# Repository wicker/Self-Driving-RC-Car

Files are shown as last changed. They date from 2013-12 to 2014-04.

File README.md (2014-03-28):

Self-Driving-RC-Car
===================

Testing out Kalman filter and SLAM code on a vehicle which can't fall out of the sky.

Hardware
--------

IMX (Imex) Firefox 1/10 scale RC car contains one RC550 brushed hobby DC motor and one three-wire RadioShack hobby servo. 

v1 controller is an Arduino Uno with VNH5019 Dual Motor Driver Carrier Shield from Pololu. 

v2 controller is an STM32F4-Discovery board with VNH5019 Dual Motor Driver Carrier shield from Pololu.

v3 controller is a custom Foxcar Control Board v1.

v4 controller is a custom Foxcar Control Board v2.

Software
--------

**v1 - Arduino**

A simple Arduino sketch to drive the motor in forward and reverse while turning the servo to steer the vehicle. Libraries used:

- [Zambetti's ASCIITable](http://arduino.cc/en/Tutorial/ASCIITable)
- [SoftwareSerial](http://arduino.cc/en/Reference/SoftwareSerial)
- [mem's ServoTimer2](http://forum.arduino.cc/index.php/topic,21975.0.html)
- [Pololu's VNH5019 Motor Driver Shield](https://github.com/pololu/dual-vnh5019-motor-shield)

**v2 - STM32F4-Discovery**

Putting everything together. 

- [Pololu's VNH5019 Motor Driver Shield](https://github.com/pololu/dual-vnh5019-motor-shield)

License
-------

Released under the 3-clause BSD. http://opensource.org/licenses/BSD-3-Clause

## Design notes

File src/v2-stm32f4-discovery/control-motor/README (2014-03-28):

INSTRUCTIONS

Add toolchain paths:

alias psas_stm="export PATH=$PATH:/opt/psas/openocd/bin:/opt/psas/x-tools/stm32f407/arm-psas-eabi/bin:/opt/eclipse/"

In this directory, modify the duration of the blinking LED pauses in main.c. 

Then:

make
st-flash write build/ch.bin 0x08000000.

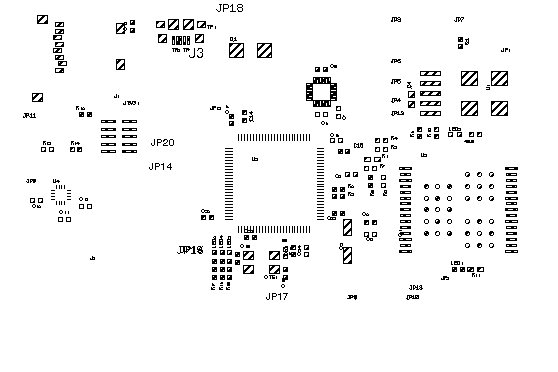
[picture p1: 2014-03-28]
sch/output.png

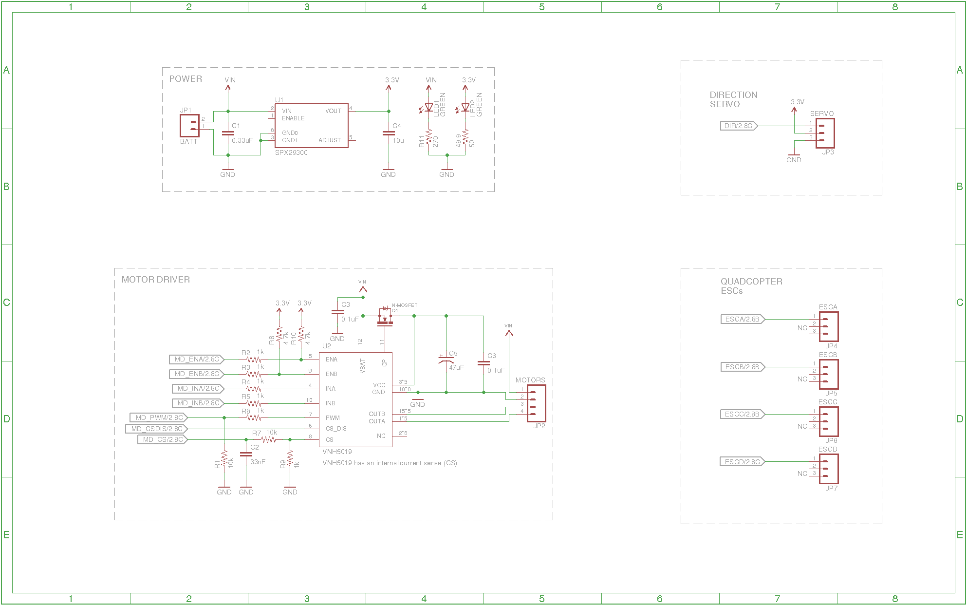
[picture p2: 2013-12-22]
sch/foxcar-control-board-sch1.png

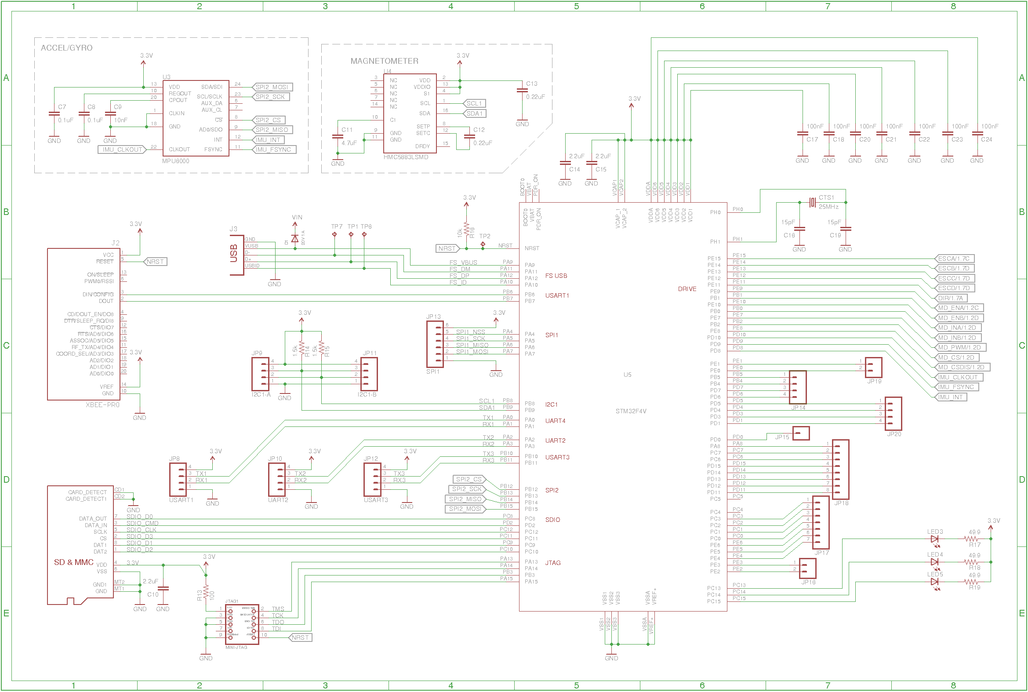
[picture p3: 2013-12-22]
sch/foxcar-control-board-sch2.png

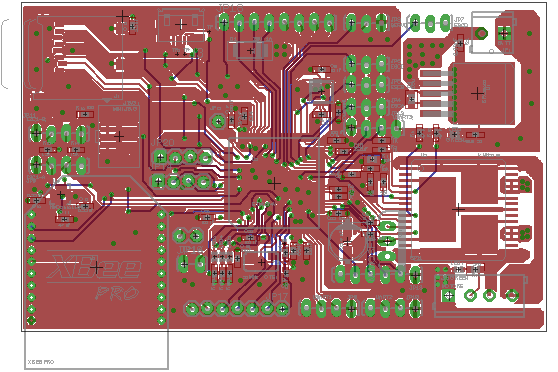
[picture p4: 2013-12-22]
sch/foxcar-control-board-brd.png

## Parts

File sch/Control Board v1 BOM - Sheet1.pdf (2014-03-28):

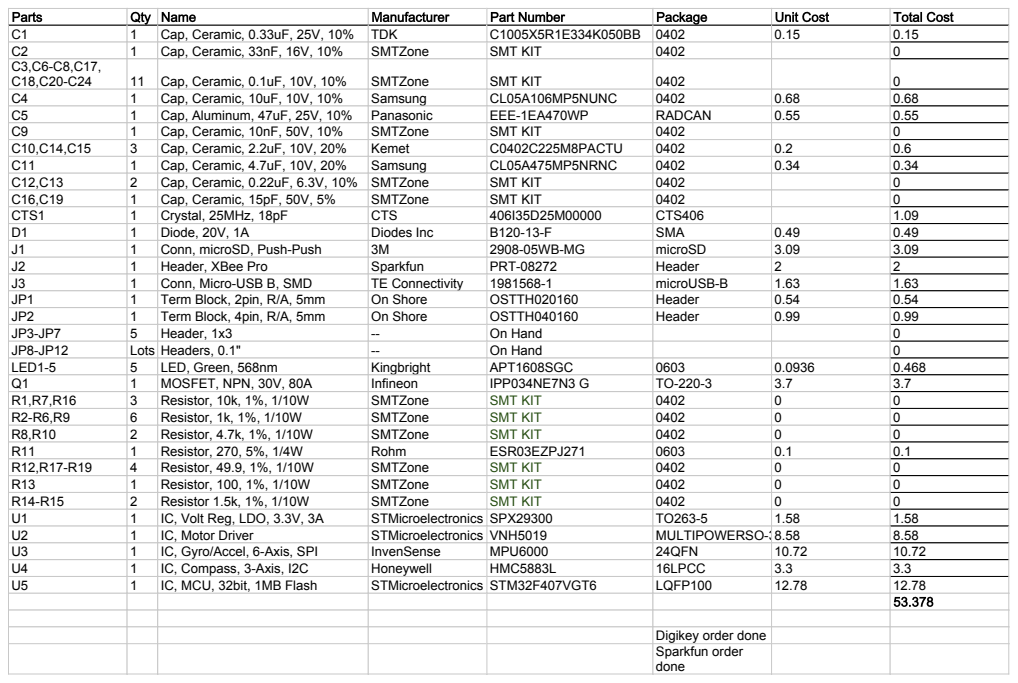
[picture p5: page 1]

Parts | Qty | Name | Manufacturer | Part Number | Package | Unit Cost | Total Cost
C1 | 1 | Cap, Ceramic, 0.33uF, 25V, 10% | TDK | C1005X5R1E334K050BB | 0402 | 0.15 | 0.15
C2 | 1 | Cap, Ceramic, 33nF, 16V, 10% | SMTZone | SMT KIT | 0402 | | 0
C3,C6-C8,C17, C18,C20-C24 | 11 | Cap, Ceramic, 0.1uF, 10V, 10% | SMTZone | SMT KIT | 0402 | | 0

C4 | 1 | Cap, Ceramic, 10uF, 10V, 10% | Samsung | CL05A106MP5NUNC | 0402 | 0.68 | 0.68
C5 | 1 | Cap, Aluminum, 47uF, 25V, 10% | Panasonic | EEE-1EA470WP | RADCAN | 0.55 | 0.55
C9 | 1 | Cap, Ceramic, 10nF, 50V, 10% | SMTZone | SMT KIT | 0402 | | 0
C10,C14,C15 | 3 | Cap, Ceramic, 2.2uF, 10V, 20% | Kemet | C0402C225M8PACTU | 0402 | 0.2 | 0.6
C11 | 1 | Cap, Ceramic, 4.7uF, 10V, 20% | Samsung | CL05A475MP5NRNC | 0402 | 0.34 | 0.34
C12,C13 | 2 | Cap, Ceramic, 0.22uF, 6.3V, 10% | SMTZone | SMT KIT | 0402 | | 0
C16,C19 | 1 | Cap, Ceramic, 15pF, 50V, 5% | SMTZone | SMT KIT | 0402 | | 0
CTS1 | 1 | Crystal, 25MHz, 18pF | CTS | 406I35D25M00000 | CTS406 | | 1.09
D1 | 1 | Diode, 20V, 1A | Diodes Inc | B120-13-F | SMA | 0.49 | 0.49
J1 | 1 | Conn, microSD, Push-Push | 3M | 2908-05WB-MG | microSD | 3.09 | 3.09
J2 | 1 | Header, XBee Pro | Sparkfun | PRT-08272 | Header | 2 | 2
J3 | 1 | Conn, Micro-USB B, SMD | TE Connectivity | 1981568-1 | microUSB-B | 1.63 | 1.63
JP1 | 1 | Term Block, 2pin, R/A, 5mm | On Shore | OSTTH020160 | Header | 0.54 | 0.54
JP2 | 1 | Term Block, 4pin, R/A, 5mm | On Shore | OSTTH040160 | Header | 0.99 | 0.99
JP3-JP7 | 5 | Header, 1x3 | -- | On Hand | | | 0
JP8-JP12 | Lots | Headers, 0.1" | -- | On Hand | | | 0
LED1-5 | 5 | LED, Green, 568nm | Kingbright | APT1608SGC | 0603 | 0.0936 | 0.468
Q1 | 1 | MOSFET, NPN, 30V, 80A | Infineon | IPP034NE7N3 G | TO-220-3 | 3.7 | 3.7
R1,R7,R16 | 3 | Resistor, 10k, 1%, 1/10W | SMTZone | SMT KIT | 0402 | 0 | 0
R2-R6,R9 | 6 | Resistor, 1k, 1%, 1/10W | SMTZone | SMT KIT | 0402 | 0 | 0
R8,R10 | 2 | Resistor, 4.7k, 1%, 1/10W | SMTZone | SMT KIT | 0402 | 0 | 0
R11 | 1 | Resistor, 270, 5%, 1/4W | Rohm | ESR03EZPJ271 | 0603 | 0.1 | 0.1
R12,R17-R19 | 4 | Resistor, 49.9, 1%, 1/10W | SMTZone | SMT KIT | 0402 | 0 | 0
R13 | 1 | Resistor, 100, 1%, 1/10W | SMTZone | SMT KIT | 0402 | 0 | 0
R14-R15 | 2 | Resistor 1.5k, 1%, 1/10W | SMTZone | SMT KIT | 0402 | 0 | 0
U1 | 1 | IC, Volt Reg, LDO, 3.3V, 3A | STMicroelectronics | SPX29300 | TO263-5 | 1.58 | 1.58
U2 | 1 | IC, Motor Driver | STMicroelectronics | VNH5019 | MULTIPOWERSO-308.58 | | 8.58
U3 | 1 | IC, Gyro/Accel, 6-Axis, SPI | InvenSense | MPU6000 | 24QFN | 10.72 | 10.72
U4 | 1 | IC, Compass, 3-Axis, I2C | Honeywell | HMC5883L | 16LPCC | 3.3 | 3.3
U5 | 1 | IC, MCU, 32bit, 1MB Flash | STMicroelectronics | STM32F407VGT6 | LQFP100 | 12.78 | 12.78

Digikey order done
Sparkfun order done

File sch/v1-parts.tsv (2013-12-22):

Parts | Qty | Name | Manufacturer | Part Number | Package
C1 | 1 | Cap, Ceramic, 0.33uF, 25V, 10% | TDK | C1005X5R1E334K050BB | 0402
C2 | 1 | Cap, Ceramic, 33nF, 16V, 10% | SMTZone | SMT KIT | 0402
C3,C6-C8,C17, C18,C20-C24 | 11 | Cap, Ceramic, 0.1uF, 10V, 10% | SMTZone | SMT KIT | 0402
C4 | 1 | Cap, Ceramic, 10uF, 10V, 10% | Samsung | CL05A106MP5NUNC | 0402
C5 | 1 | Cap, Aluminum, 47uF, 25V, 10% | Panasonic | EEE-1EA470WP | RADCAN
C9 | 1 | Cap, Ceramic, 10nF, 50V, 10% | SMTZone | SMT KIT | 0402
C10,C14,C15 | 3 | Cap, Ceramic, 2.2uF, 10V, 20% | Kemet | C0402C225M8PACTU | 0402
C11 | 1 | Cap, Ceramic, 4.7uF, 10V, 20% | Samsung | CL05A475MP5NRNC | 0402
C12,C13 | 2 | Cap, Ceramic, 0.22uF, 6.3V, 10% | SMTZone | SMT KIT | 0402
C16,C19 | 1 | Cap, Ceramic, 15pF, 50V, 5% | SMTZone | SMT KIT | 0402
CTS1 | 1 | Crystal, 25MHz, 18pF | CTS | 406I35D25M00000 | CTS406
D1 | 1 | Diode, 20V, 1A | Diodes Inc | B120-13-F | SMA
J1 | 1 | Conn, microSD, Push-Push | 3M | 2908-05WB-MG | microSD
J2 | 1 | Header, XBee Pro | Sparkfun | PRT-08272 | Header
J3 | 1 | Conn, Micro-USB B, SMD | TE Connectivity | 1981568-1 | microUSB-B
JP1 | 1 | Term Block, 2pin, R/A, 5mm | On Shore | OSTTH020160 | Header
JP2 | 1 | Term Block, 4pin, R/A, 5mm | On Shore | OSTTH040160 | Header
JP3-JP7 | 5 | Header, 1x3 | -- | On Hand
JP8-JP12 | Lots | Headers, 0.1in | -- | On Hand
LED1-5 | 5 | LED, Green, 568nm | Kingbright | APT1608SGC | 0603
Q1 | 1 | MOSFET, NPN, 30V, 80A | Infineon | IPP034NE7N3 G | TO-220-3
R1,R7,R16 | 3 | Resistor, 10k, 1%, 1/10W | SMTZone | SMT KIT | 0402
R2-R6,R9 | 6 | Resistor, 1k, 1%, 1/10W | SMTZone | SMT KIT | 0402
R8,R10 | 2 | Resistor, 4.7k, 1%, 1/10W | SMTZone | SMT KIT | 0402
R11 | 1 | Resistor, 270, 5%, 1/4W | Rohm | ESR03EZPJ271 | 0603
R12,R17-R19 | 4 | Resistor, 49.9, 1%, 1/10W | SMTZone | SMT KIT | 0402
R13 | 1 | Resistor, 100, 1%, 1/10W | SMTZone | SMT KIT | 0402
R14-R15 | 2 | Resistor 1.5k, 1%, 1/10W | SMTZone | SMT KIT | 0402
U1 | 1 | IC, Volt Reg, LDO, 3.3V, 3A | STMicroelectronics | SPX29300 | TO263-5
U2 | 1 | IC, Motor Driver | STMicroelectronics | VNH5019 | MULTIPOWERSO-30
U3 | 1 | IC, Gyro/Accel, 6-Axis, SPI | InvenSense | MPU6000 | 24QFN
U4 | 1 | IC, Compass, 3-Axis, I2C | Honeywell | HMC5883L | 16LPCC
U5 | 1 | IC, MCU, 32bit, 1MB Flash | STMicroelectronics | STM32F407VGT6 | LQFP100

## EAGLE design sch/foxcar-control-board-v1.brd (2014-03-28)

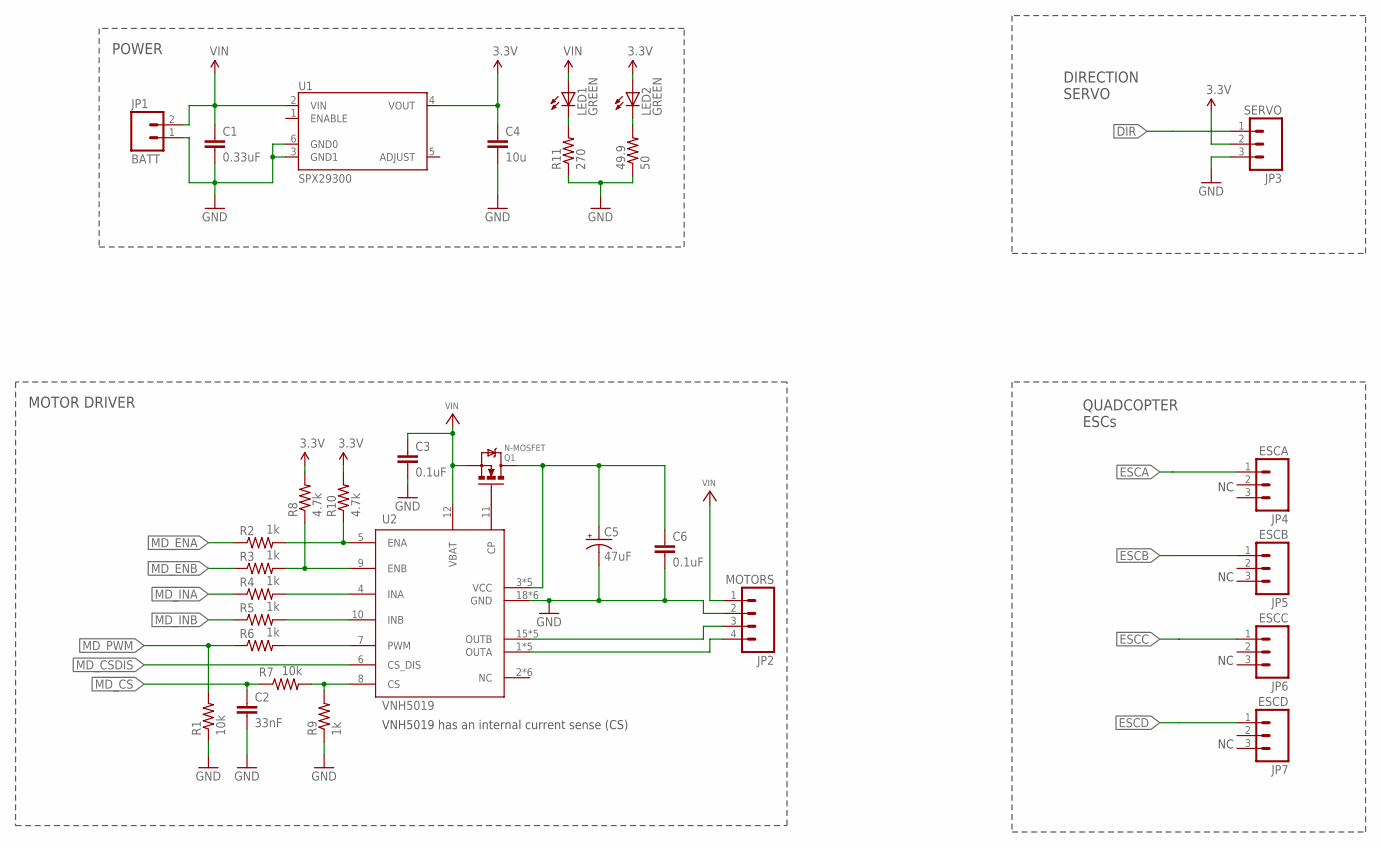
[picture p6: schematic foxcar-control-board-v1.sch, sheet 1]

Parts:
49.9: 50; 0402-RES
C1: 0.33uF; 0402-CAP
C2: 33nF; 0402-CAP
C3, C6: 0.1uF; 0402-CAP
C4: 10u; 0603-CAP
C5: 47uF; PANASONIC_D
JP1: BATT; SCREWTERMINAL-3.5MM-2_LOCK
JP2: MOTORS; SCREWTERMINAL-3.5MM-4_LOCK
JP3: SERVO; 1X03_LOCK_LONGPADS
JP4: ESCA; 1X03_LOCK_LONGPADS
JP5: ESCB; 1X03_LOCK_LONGPADS
JP6: ESCC; 1X03_LOCK_LONGPADS
JP7: ESCD; 1X03_LOCK_LONGPADS
LED1, LED2: GREEN; CHIPLED_0603
Q1: N-MOSFET; TO220V
R1: 10k; 0603-RES
R2, R3, R4, R5, R6, R9: 1k; 0402-RES
R7: 10k; 0402-RES
R8, R10: 4.7k; 0402-RES
R11: 270; 0603-RES
U1: SPX29300; TO263-5
U2: VNH5019; MULTIPOWERSO-30

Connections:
3.3V: C4.1, JP3.2, LED2.A, R8.2, R10.2, U1.4 (VOUT); also elsewhere on the board
CP: Q1.1 (G), U2.11 (CP)
CS: R7.2, R9.2, U2.8 (CS)
DIR: JP3.1; also elsewhere on the board
ENA: R2.2, R10.1, U2.5 (ENA)
ENB: R3.2, R8.1, U2.9 (ENB)
ESCA: JP4.1; also elsewhere on the board
ESCB: JP5.1; also elsewhere on the board
ESCC: JP6.1; also elsewhere on the board
ESCD: JP7.1; also elsewhere on the board
GND: 49.9.1, C1.2, C2.2, C3.2, C4.2, C5.-, C6.2, JP1.1, JP2.2, JP3.3, R1.1, R9.1, R11.1, U1.3 (GND1), U1.6 (GND0), U2.18 (GND), U2.19 (GND), U2.20 (GND), U2.26 (GND), U2.27 (GND), U2.28 (GND); also elsewhere on the board
INA: R4.2, U2.4 (INA)
INB: R5.2, U2.10 (INB)
MD_CS: C2.1, R7.1; also elsewhere on the board
MD_CSDIS: U2.6 (CS_DIS); also elsewhere on the board
MD_ENA: R2.1; also elsewhere on the board
MD_ENB: R3.1; also elsewhere on the board
MD_INA: R4.1; also elsewhere on the board
MD_INB: R5.1; also elsewhere on the board
MD_PWM: R1.2, R6.1; also elsewhere on the board
unnamed: 49.9.2, LED2.C
unnamed: LED1.C, R11.2
OUTA: JP2.4, U2.1 (OUTA), U2.25 (OUTA), U2.30 (OUTA), U2.OUTA, U2.OUTA@1 (OUTA)
OUTB: JP2.3, U2.15 (OUTB), U2.16 (OUTB), U2.21 (OUTB), U2.OUTB, U2.OUTB@1 (OUTB)
PWM: R6.2, U2.7 (PWM)
VCC: C5.+, C6.1, Q1.2 (D), U2.3 (VCC), U2.13 (VCC), U2.23 (VCC), U2.VCC, U2.VCC@1 (VCC)
VIN: C1.1, C3.1, JP1.2, JP2.1, LED1.A, Q1.3 (S), U1.2 (VIN), U2.12 (VBAT); also elsewhere on the board

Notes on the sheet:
VNH5019 has an internal current sense (CS)
POWER
MOTOR DRIVER
DIRECTION SERVO
QUADCOPTER ESCs

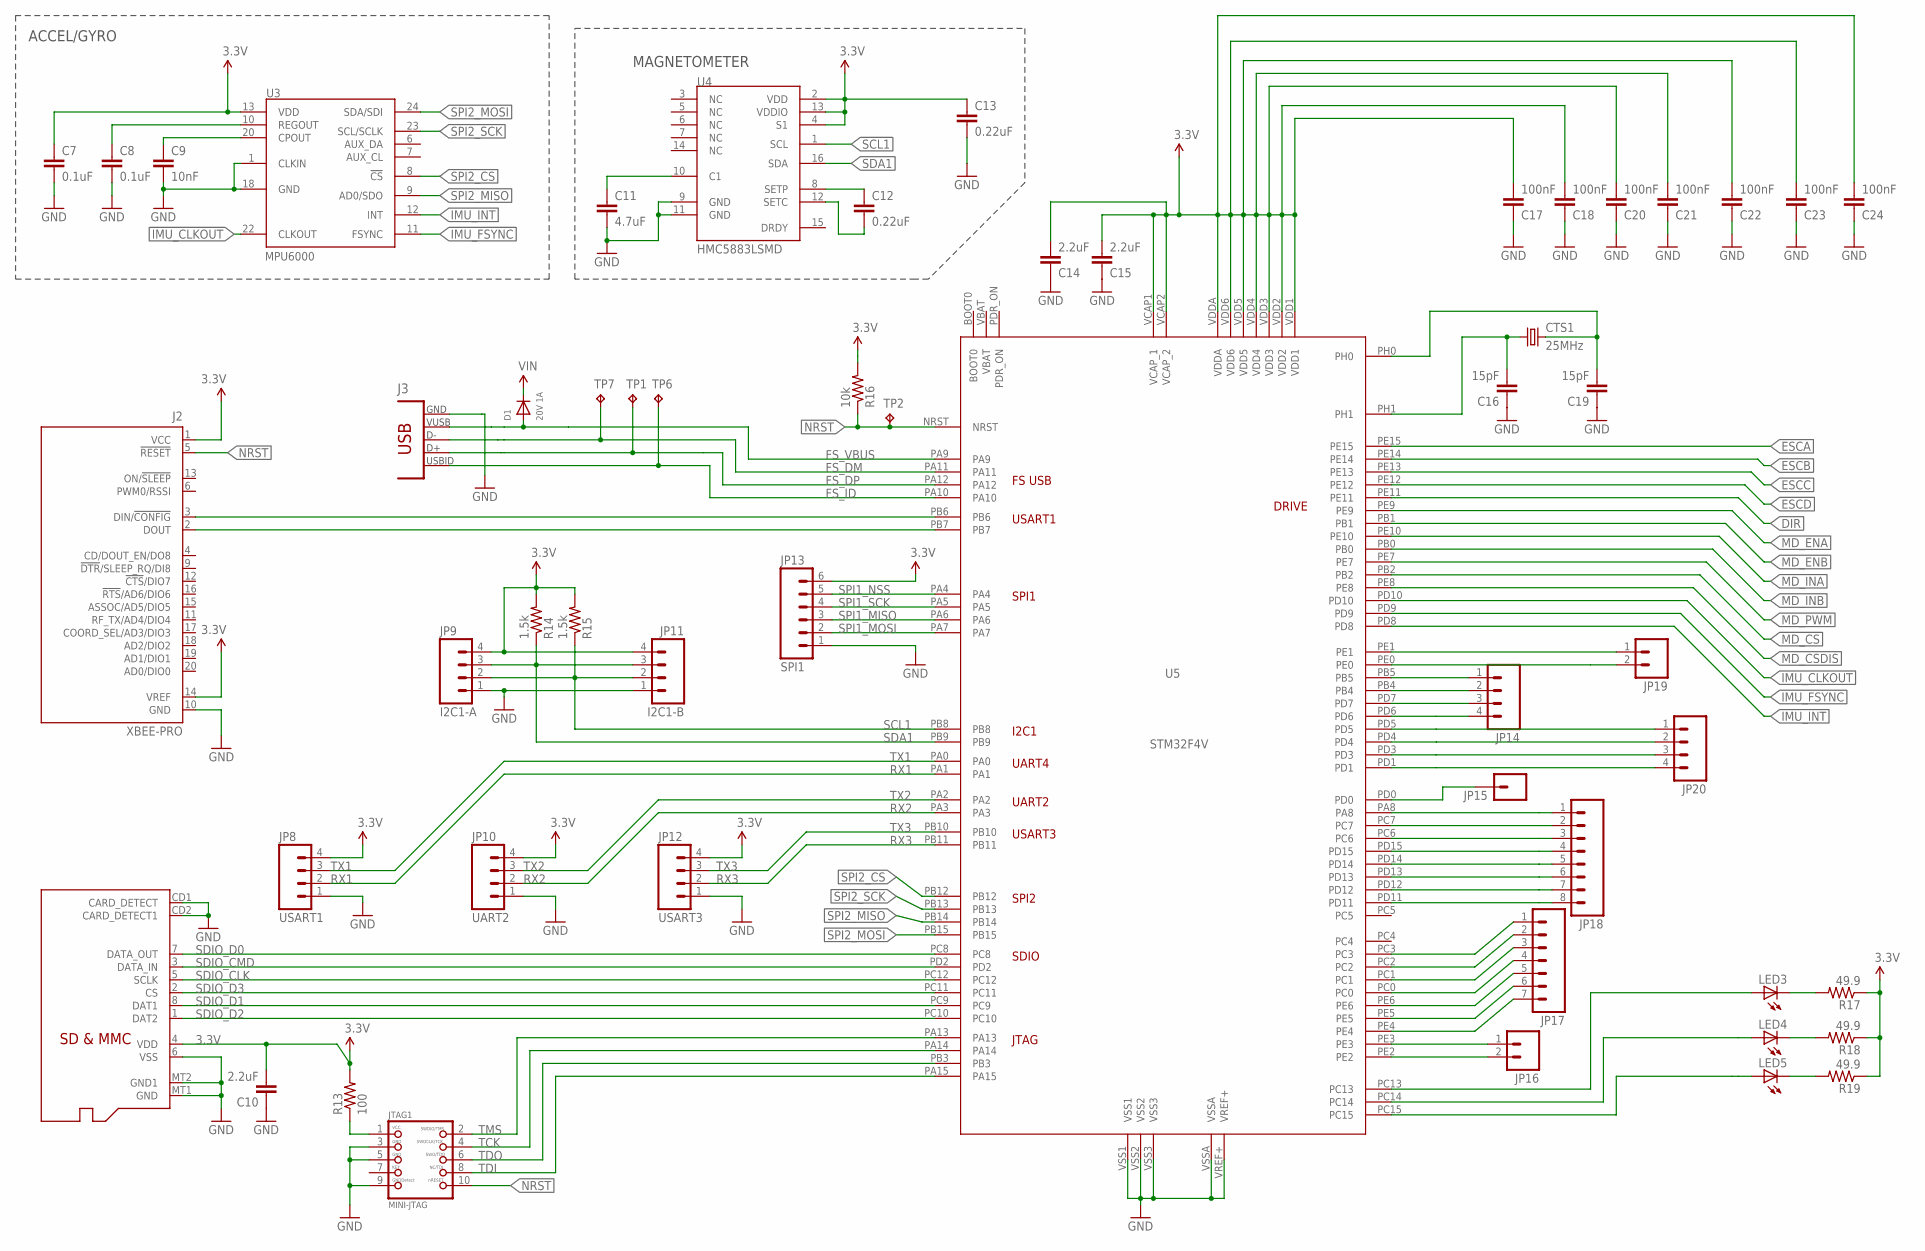
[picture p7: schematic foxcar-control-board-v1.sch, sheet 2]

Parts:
C7, C8: 0.1uF; 0402-CAP
C9: 10nF; 0402-CAP
C10, C14, C15: 2.2uF; 0402-CAP
C11: 4.7uF; 0402-CAP
C12, C13: 0.22uF; 0402-CAP
C16, C19: 15pF; 0402-CAP
C17, C18, C20, C21, C22, C23, C24: 100nF; 0402-CAP
CTS1: 25MHz; CTS406
D1: 20V 1A; SMADIODE
J1: MICROSD
J2: XBEE-PRO
J3: CON-USB-F-MICRO-B; CONN_USB_MICRO-B
JP8: USART1; 1X04_LOCK_LONGPADS
JP9: I2C1-A; 1X04_LOCK_LONGPADS
JP10: UART2; 1X04_LOCK_LONGPADS
JP11: I2C1-B; 1X04_LOCK_LONGPADS
JP12: USART3; 1X04_LOCK_LONGPADS
JP13: SPI1; 1X06_LOCK_LONGPADS
JP14, JP20: M04LOCK; 1X04_LOCK
JP15: M01PTH; 1X01
JP16: M02LOCK_LONGPADS; 1X02_LOCK_LONGPADS
JP17: M07LOCK; 1X07_LOCK
JP18: M08LOCK_LONGPADS; 1X08_LOCK_LONGPADS
JP19: M02LOCK; 1X02_LOCK
JTAG1: MINI-JTAG; 2X05_1.27MM_SMT
LED3, LED4, LED5: LEDCHIPLED_0603; CHIPLED_0603
R13: 100; 0402-RES
R14, R15: 1.5k; 0402-RES
R16: 10k; 0402-RES
R17, R18, R19: 49.9; 0402-RES
TP1, TP2, TP6, TP7: TPTP06R; TP06R
U3: MPU6000; QFN.24.4X4
U4: HMC5883LSMD; 16LPCC
U5: STM32F4V; LQFP100

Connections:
3.3V: C7.1, C10.2, C13.1, C14.2, C15.2, C17.2, C18.2, C20.2, C21.2, C22.2, C23.2, C24.2, J1.4 (VDD), J2.1 (VCC), J2.14 (VREF), JP8.4, JP9.4, JP10.4, JP11.4, JP12.4, JP13.6, R13.2, R14.2, R15.2, R16.2, R17.1, R18.1, R19.1, U3.13 (VDD), U4.2 (VDD), U4.4 (S1), U4.13 (VDDIO), U5.VCAP1 (VCAP_1), U5.VCAP2 (VCAP_2), U5.VDD1, U5.VDD2, U5.VDD3, U5.VDD4, U5.VDD5, U5.VDD6, U5.VDDA; also elsewhere on the board
DIR: U5.PE11; also elsewhere on the board
ESCA: U5.PE15; also elsewhere on the board
ESCB: U5.PE14; also elsewhere on the board
ESCC: U5.PE13; also elsewhere on the board
ESCD: U5.PE12; also elsewhere on the board
FS_DM: J3.P2 (D-), TP7.TP, U5.PA11
FS_DP: J3.P3 (D+), TP1.TP, U5.PA12
FS_ID: J3.P4 (USBID), TP6.TP, U5.PA10
FS_VBUS: D1.A, J3.P1 (VUSB), U5.PA9
GND: C7.2, C8.2, C9.2, C10.1, C11.2, C13.2, C14.1, C15.1, C16.1, C17.1, C18.1, C19.1, C20.1, C21.1, C22.1, C23.1, C24.1, J1.6 (VSS), J1.CD1 (CARD_DETECT), J1.CD2 (CARD_DETECT1), J1.MT1 (GND), J1.MT2 (GND1), J2.10 (GND), J3.P5 (GND), JP8.1, JP9.1, JP10.1, JP11.1, JP12.1, JP13.1, JTAG1.3, JTAG1.5, JTAG1.9, U3.1 (CLKIN), U3.18 (GND), U4.9 (GND), U4.11 (GND), U5.VREF+, U5.VSS1, U5.VSS2, U5.VSS3, U5.VSSA; also elsewhere on the board
IMU_CLKOUT: U3.22 (CLKOUT), U5.PD10
IMU_FSYNC: U3.11 (FSYNC), U5.PD9
IMU_INT: U3.12 (INT), U5.PD8
LED_B: LED5.A, U5.PC15
LED_G: LED4.A, U5.PC14
LED_R: LED3.A, U5.PC13
MD_CS: U5.PB2; also elsewhere on the board
MD_CSDIS: U5.PE8; also elsewhere on the board
MD_ENA: U5.PE9; also elsewhere on the board
MD_ENB: U5.PB1; also elsewhere on the board
MD_INA: U5.PE10; also elsewhere on the board
MD_INB: U5.PB0; also elsewhere on the board
MD_PWM: U5.PE7; also elsewhere on the board
unnamed: JP18.1, U5.PA8
unnamed: C12.2, U4.12 (SETC)
unnamed: LED3.C, R17.2
unnamed: LED4.C, R18.2
unnamed: LED5.C, R19.2
unnamed: JP17.4, U5.PC0
unnamed: JP17.3, U5.PC1
unnamed: C12.1, U4.8 (SETP)
unnamed: C11.1, U4.10 (C1)
unnamed: JP17.2, U5.PC2
unnamed: JP19.1, U5.PE1
unnamed: JP17.1, U5.PC3
unnamed: C9.1, U3.20 (CPOUT)
unnamed: JTAG1.1, R13.1
unnamed: JP16.2, U5.PE2
unnamed: JP16.1, U5.PE3
unnamed: JP17.7, U5.PE4
unnamed: JP17.6, U5.PE5
unnamed: JP17.5, U5.PE6
unnamed: JP18.2, U5.PC7
unnamed: JP18.3, U5.PC6
unnamed: JP18.4, U5.PD15
unnamed: JP18.5, U5.PD14
unnamed: JP18.6, U5.PD13
unnamed: JP18.7, U5.PD12
unnamed: JP18.8, U5.PD11
unnamed: JP19.2, U5.PE0
unnamed: JP14.1, U5.PB5
unnamed: JP14.2, U5.PB4
unnamed: JP14.3, U5.PD7
unnamed: JP14.4, U5.PD6
unnamed: JP20.1, U5.PD5
unnamed: JP20.2, U5.PD4
unnamed: JP20.3, U5.PD3
unnamed: JP20.4, U5.PD1
unnamed: JP15.1, U5.PD0
NRST: J2.5 (!RESET), JTAG1.10, R16.1, TP2.TP, U5.NRST
OSC_IN1: C19.2, CTS1.3 (2), U5.PH0
OSC_OUT1: C16.2, CTS1.1, U5.PH1
REGOUT: C8.1, U3.10 (REGOUT)
RX1: JP8.2, U5.PA1
RX2: JP10.2, U5.PA3
RX3: JP12.2, U5.PB11
RX_DOUT1: J2.2 (DOUT), U5.PB7
SCL1: JP9.2, JP11.2, R15.1, U4.1 (SCL), U5.PB8
SDA1: JP9.3, JP11.3, R14.1, U4.16 (SDA), U5.PB9
SDIO_CLK: J1.5 (SCLK), U5.PC12
SDIO_CMD: J1.3 (DATA_IN), U5.PD2
SDIO_D0: J1.7 (DATA_OUT), U5.PC8
SDIO_D1: J1.8 (DAT1), U5.PC9
SDIO_D2: J1.1 (DAT2), U5.PC10
SDIO_D3: J1.2 (CS), U5.PC11
SPI1_MISO: JP13.3, U5.PA6
SPI1_MOSI: JP13.2, U5.PA7
SPI1_NSS: JP13.5, U5.PA4
SPI1_SCK: JP13.4, U5.PA5
SPI2_CS: U3.8 (!CS), U5.PB12
SPI2_MISO: U3.9 (AD0/SDO), U5.PB14
SPI2_MOSI: U3.24 (SDA/SDI), U5.PB15
SPI2_SCK: U3.23 (SCL/SCLK), U5.PB13
TCK: JTAG1.4, U5.PA14
TDI: JTAG1.8, U5.PA15
TDO: JTAG1.6, U5.PB3
TMS: JTAG1.2, U5.PA13
TX1: JP8.3, U5.PA0
TX2: JP10.3, U5.PA2
TX3: JP12.3, U5.PB10
TX_DIN1: J2.3 (DIN/!CONFIG), U5.PB6
VIN: D1.C; also elsewhere on the board

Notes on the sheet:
ACCEL/GYRO
MAGNETOMETER

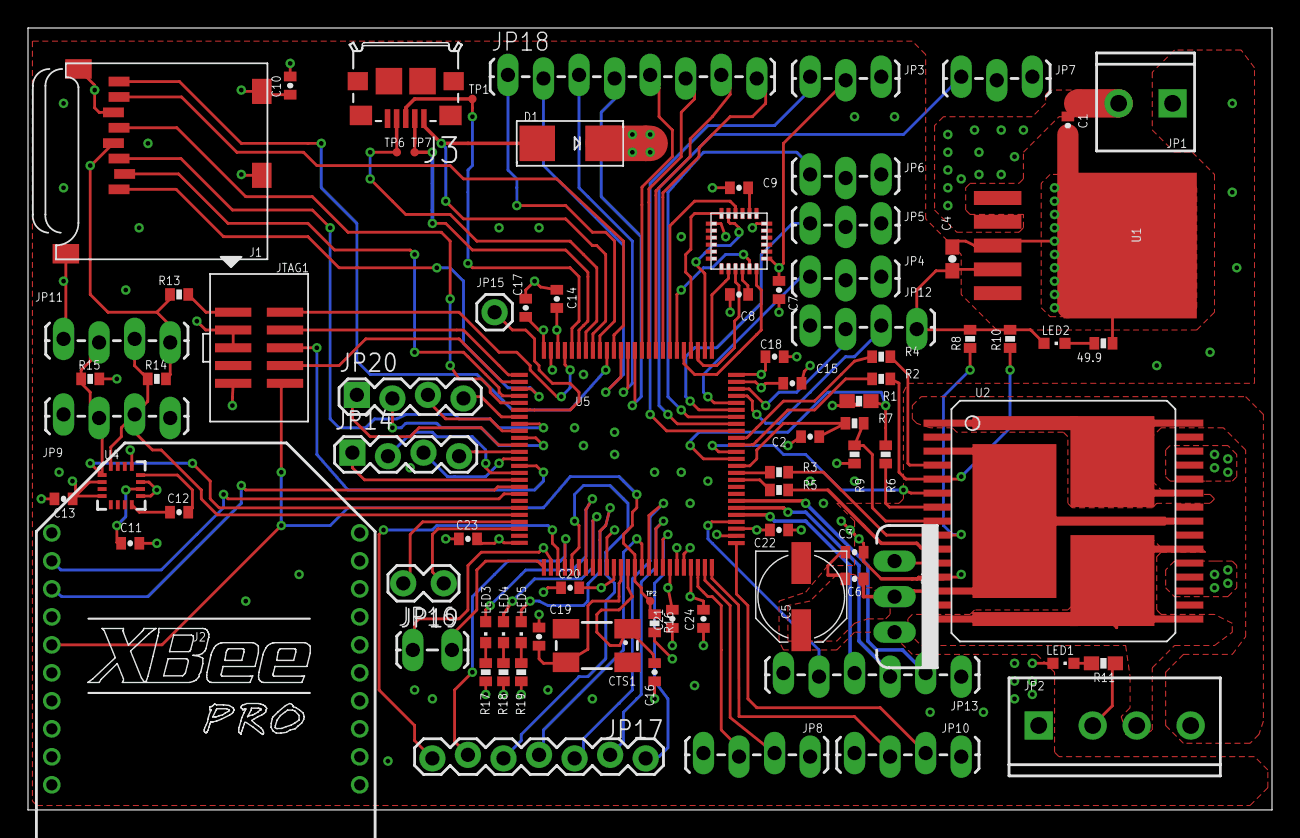
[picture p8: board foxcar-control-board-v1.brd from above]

Board: 4 copper layers, 88.9 x 55.9 mm, 84 parts (0 on the bottom side), 105 nets.

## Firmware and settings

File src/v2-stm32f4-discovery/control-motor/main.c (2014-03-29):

// Servo control
//
// Servo on pin PB8 uses TIM4 channel 3 on alternate function 2
// TIM4 supports PWM driving.
// PWMD4 is a HAL-defined driver associated with TIM4.
 
#include "ch.h"
#include "hal.h"
 
#define LEFT 0
#define RIGHT 1

#define INAPIN 1 // PB1
#define INBPIN 2 // PB2
 
static PWMConfig pwmcfg = {
  1000000, // 1MHz PWM clock
  20000, // PWM period 20ms 
  NULL, // No callback 
  {
    {PWM_OUTPUT_DISABLED, NULL},      
    {PWM_OUTPUT_DISABLED, NULL},     
    {PWM_OUTPUT_ACTIVE_HIGH, NULL},   
    {PWM_OUTPUT_DISABLED, NULL},       
  },
  0
};
 
int main(void)
{
  halInit();
  chSysInit();
  
  palSetPadMode(GPIOB, 0, PAL_MODE_ALTERNATE(2)); // alt mode is PWM-enabled TIM3
  palSetPadMode(GPIOB, INAPIN, PAL_MODE_OUTPUT_PUSHPULL); // set INA to be an output
  palSetPadMode(GPIOB, INBPIN, PAL_MODE_OUTPUT_PUSHPULL); // set INB to be an output
   
  pwmStart(&PWMD3, &pwmcfg); // TIM3 for motors
 
  while (TRUE) {
    // one direction (possibly forward)
    pwmEnableChannel(&PWMD3, 3, 500);
    palSetPad(GPIOB, INAPIN);
    palClearPad(GPIOB, INBPIN);
    chThdSleepMilliseconds(3000);

    // the other direction (possibly backward)
    pwmEnableChannel(&PWMD3, 3, 500);
    palSetPad(GPIOB, INBPIN);
    palClearPad(GPIOB, INAPIN);
    chThdSleepMilliseconds(3000);
  }
}

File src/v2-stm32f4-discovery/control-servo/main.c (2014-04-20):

// Servo control
//
// TIM4 supports PWM driving.
// Servo on pin PB8 uses TIM4 channel 3 on alternate function 2
// PWMD4 is a HAL-defined driver associated with TIM4.
 
#include "ch.h"
#include "hal.h"
 
#define LEFT 0
#define RIGHT 1
 
static PWMConfig pwmcfg = {
  1000000, // 1MHz PWM clock
  20000, // PWM period 20ms 
  NULL, // No callback 
  {
    {PWM_OUTPUT_DISABLED, NULL},      
    {PWM_OUTPUT_DISABLED, NULL},     
    {PWM_OUTPUT_ACTIVE_HIGH, NULL},   
    {PWM_OUTPUT_DISABLED, NULL},       
  },
  0
};
 
int main(void)
{
  static int step = 100, width = 500; /* starts at .7ms, ends at 2.5ms */
 
  halInit();
  chSysInit();
  
  // sets alternate mode 2 which is TIM4 
  palSetPadMode(GPIOB, 8, PAL_MODE_ALTERNATE(2));
   
  pwmStart(&PWMD4, &pwmcfg);
 
  while (TRUE) {
    pwmEnableChannel(&PWMD4, 2, width);
    // if all the way to the left or right, go back the way you came
    if (width <= 700) step = 100;
    else if (width >= 2500) step = -100;
    // now increment the width by step
    width += step;
    // brief delay
    chThdSleepMilliseconds(100);
  }
}

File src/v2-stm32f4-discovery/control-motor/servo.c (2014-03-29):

/*
 * ChibiOS/Servo is a small library to easily interface RC servos with ChibiOS/RT.
 *
 * BSD licensed
 *
 * Author: Joel Bodenmann aka Tectu   <joel@unormal.org>
 */

#include "servo.h"

static PWMConfig pwmcfg = {
    1000000,	// 1MHz PWM clock frequency
    20000,		// PWM period 20 milliseconds
  	NULL,		// no callback
  	{NULL},		// channel configuration set dynamicall in servoInit()
    0,
    0
};

void servoInit(Servo *servo) {
	/* create the channel configuration */
	PWMChannelConfig chcfg = { PWM_OUTPUT_ACTIVE_HIGH, NULL };
	pwmcfg.channels[servo->pwm_channel] = chcfg;

	/* configure PAL */
//	#if defined(STM32F1XX)
//		palSetPadMode(servo->port, servo->pin, PAL_MiODE_STM32_ALTERNATE_PUSHPULL);
  palSetPadMode(GPIOB,9,PAL_MODE_OUTPUT_PUSHPULL);
//	#else
//		#error "PAL configuration for this device not implemented yet - Please modify servoInit()"
//	#endif

	/* start the PWM unit */
	pwmStart(servo->pwm_driver, &pwmcfg);
}

void servoSetValue(Servo *servo, uint16_t value) {
	/* a bit of safty here */
	if(value > servo->max)
		value = servo->max;
	if(value < servo->min)
		value = servo->min;

	pwmEnableChannel(servo->pwm_driver, servo->pwm_channel, (pwmcnt_t)value);
}

void servoSetMax(Servo *servo, uint16_t value) {
	servo->max = value;	
}

void servoSetMin(Servo *servo, uint16_t value) {
	servo->min = value;
}

uint16_t servoGetMax(Servo *servo) {
	return (servo->max);
}

uint16_t servoGetMin(Servo *servo) {
	return (servo->min);
}

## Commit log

2012-10-09 Basic outline of a basic Kalman filter.
2012-10-21 File takes command line inputs of filter type and value of T.
2012-11-15 Filter finished. All math is includedin filter/use_kf.c. Needs to be pulled out into matrix header.
2013-11-11 Modded an RC car. Motor and servo control test complete.
2013-11-23 Pubs and start of a schematic.
    [foxcar-control-board-v1.sch]
2013-11-24 Power and voltage regs done. Started current sense.
    [foxcar-control-board-v1.sch]
2013-11-25 Added IMU sensors (gyro, accel, compass) using Sparkfun references.
    [foxcar-control-board-v1.sch]
2013-11-28 Added custom STM32F4 64-pin symbol and device to layout.
    [foxcar-control-board-v1.sch]
2013-11-28 Added most of sheet 3 stm32f4 with all its connections.
    [foxcar-control-board-v1.sch]
2013-11-28 Tested the Maxbotix EZ4, then added it to sheet 3. Wires in place, still need Rs and Cs.
    [foxcar-control-board-v1.sch]
2013-12-09 Schematic done! Passes ERC.
    [foxcar-control-board-v1.sch]
2013-12-10 Info added. Small cleanups.
    [foxcar-control-board-v1.sch]
2013-12-10 The last of the ERCs. Chose diode and LEDs.
    [foxcar-control-board-v1.sch]
2013-12-10 Set up Eagle board with Sparkfun 4-layer DRU. Set up layers. Started with power section.
    [foxcar-control-board-v1.brd, foxcar-control-board-v1.sch]
2013-12-13 Almost done with power layout. Minor stm32 symbol changes.
    [foxcar-control-board-v1.brd, foxcar-control-board-v1.sch]
2013-12-14 Making progress on layout.
    [foxcar-control-board-v1.brd, foxcar-control-board-v1.sch]
2013-12-15 Going to set aside that layout and try a fresh start.
    [foxcar-control-board-v1.brd, foxcar-control-board-v1.sch]
2013-12-15 Trying a new technique: placing all components around the stm32f4 with relatively direct paths, then seeing how badly I can fuck it up.
    [foxcar-control-board-v1.brd, foxcar-control-board-v1.sch]
2013-12-15 Making much better progress on stm32. relocating to house because I live in a land of less-than-24-hour coffee shops. :(
    [foxcar-control-board-v1.brd, foxcar-control-board-v1.sch]
2013-12-15 Everything laid out except for the power stuff.
    [foxcar-control-board-v1.brd, foxcar-control-board-v1.sch]
2013-12-15 Layout done, screenshots uploaded, parts list added.
    [foxcar-control-board-v1.brd, foxcar-control-board-v1.sch]
2013-12-20 Added library for this repo.
    [foxcar-control-board-v1.brd, foxcar-control-board-v1.sch]
2013-12-22 Made BOM and had to make some changes. Final parts list included.
    [foxcar-control-board-v1.brd, foxcar-control-board-v1.sch, v1-parts.tsv]
2013-12-22 Making TSV file all prettified.
    [v1-parts.tsv]
2013-12-30 Added a couple of basic serial tests from Ladyada and Arduino.
2013-12-30 Remote control of on-car servo via XBees from minicom.
2014-03-28 Ready for control board build.
    [foxcar-control-board-v1.brd, foxcar-control-board-v1.sch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]
2014-03-28 Ignoring build folder in stm32 projects.
2014-03-28 Ignoring .dep folder in stm32 projects.
2014-03-29 Added PWM-driven LED and PWM-driven servo to stm32f4.
2014-03-29 Testing servo and motor control code.
2014-04-20 Verified this code works with Arduino, VNH5019, and STM32F4 running onboard car.

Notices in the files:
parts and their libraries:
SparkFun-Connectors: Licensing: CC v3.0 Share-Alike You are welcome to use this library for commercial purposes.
